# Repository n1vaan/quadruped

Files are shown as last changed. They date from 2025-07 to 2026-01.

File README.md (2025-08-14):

# Quadruped Robot

### Project Description

This is a smart quadruped robot dog that imitates the Boston Dynamics robot Spot. It uses inverse kinematics logic, along with visual input through cameras and quantitive measurements through an IMU to inform it's walking and movement algorithmns. 

### Why we made it

We set out to build a quadruped robot to better understand how complex systems like locomotion, balance, and perception work together in robotics. This project gave us the opportunity to apply concepts like inverse kinematics, sensor integration, and real-time control in a hands-on way. Building a walking robot also pushed us to think carefully about both mechanical design and software logic.

## Fully Assembled Prototype 
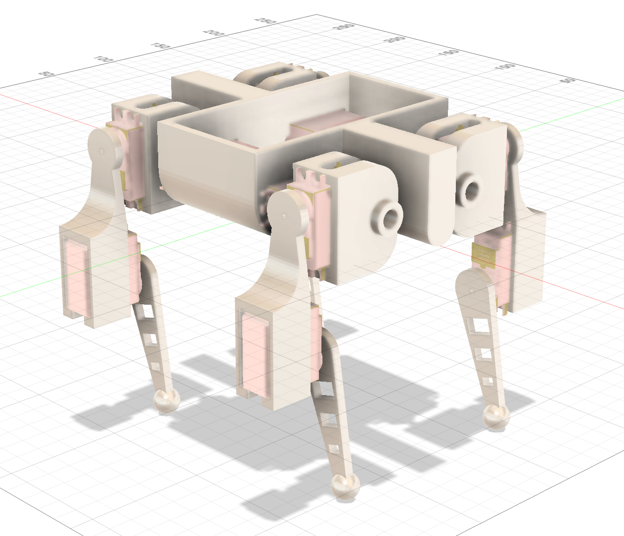
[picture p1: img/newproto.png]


## Rendered Prototype 
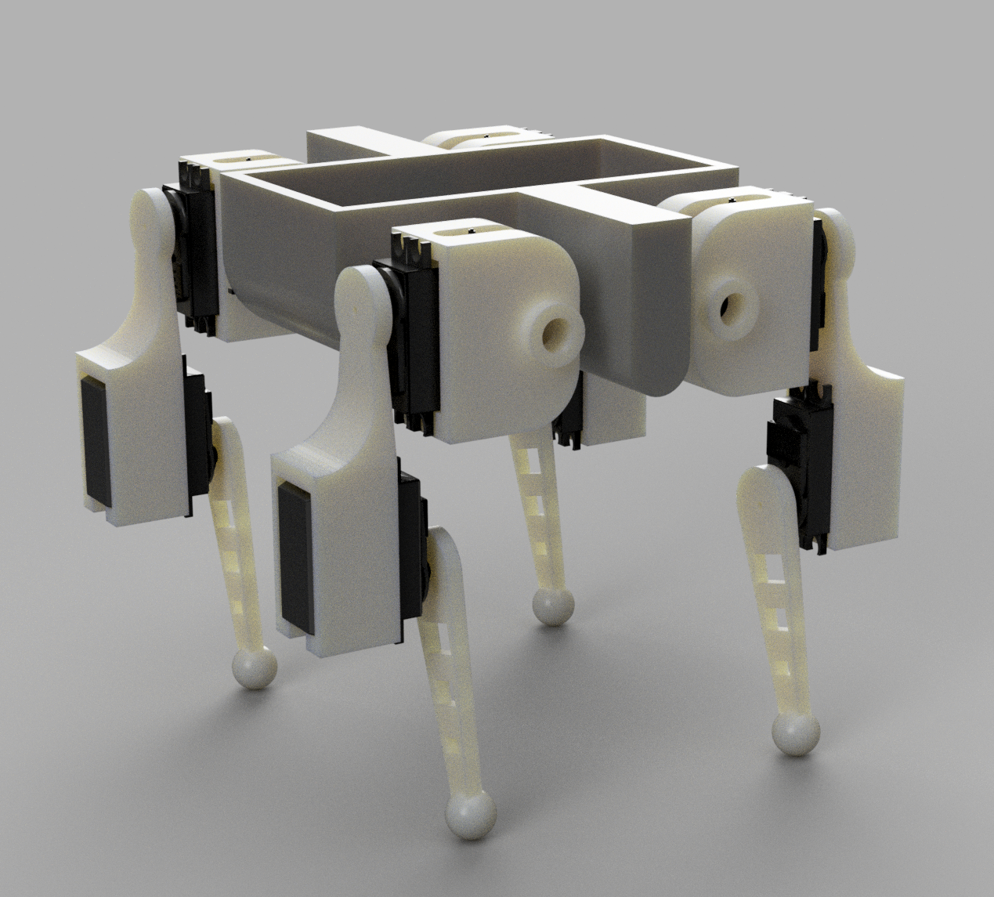
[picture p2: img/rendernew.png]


## Circuit 
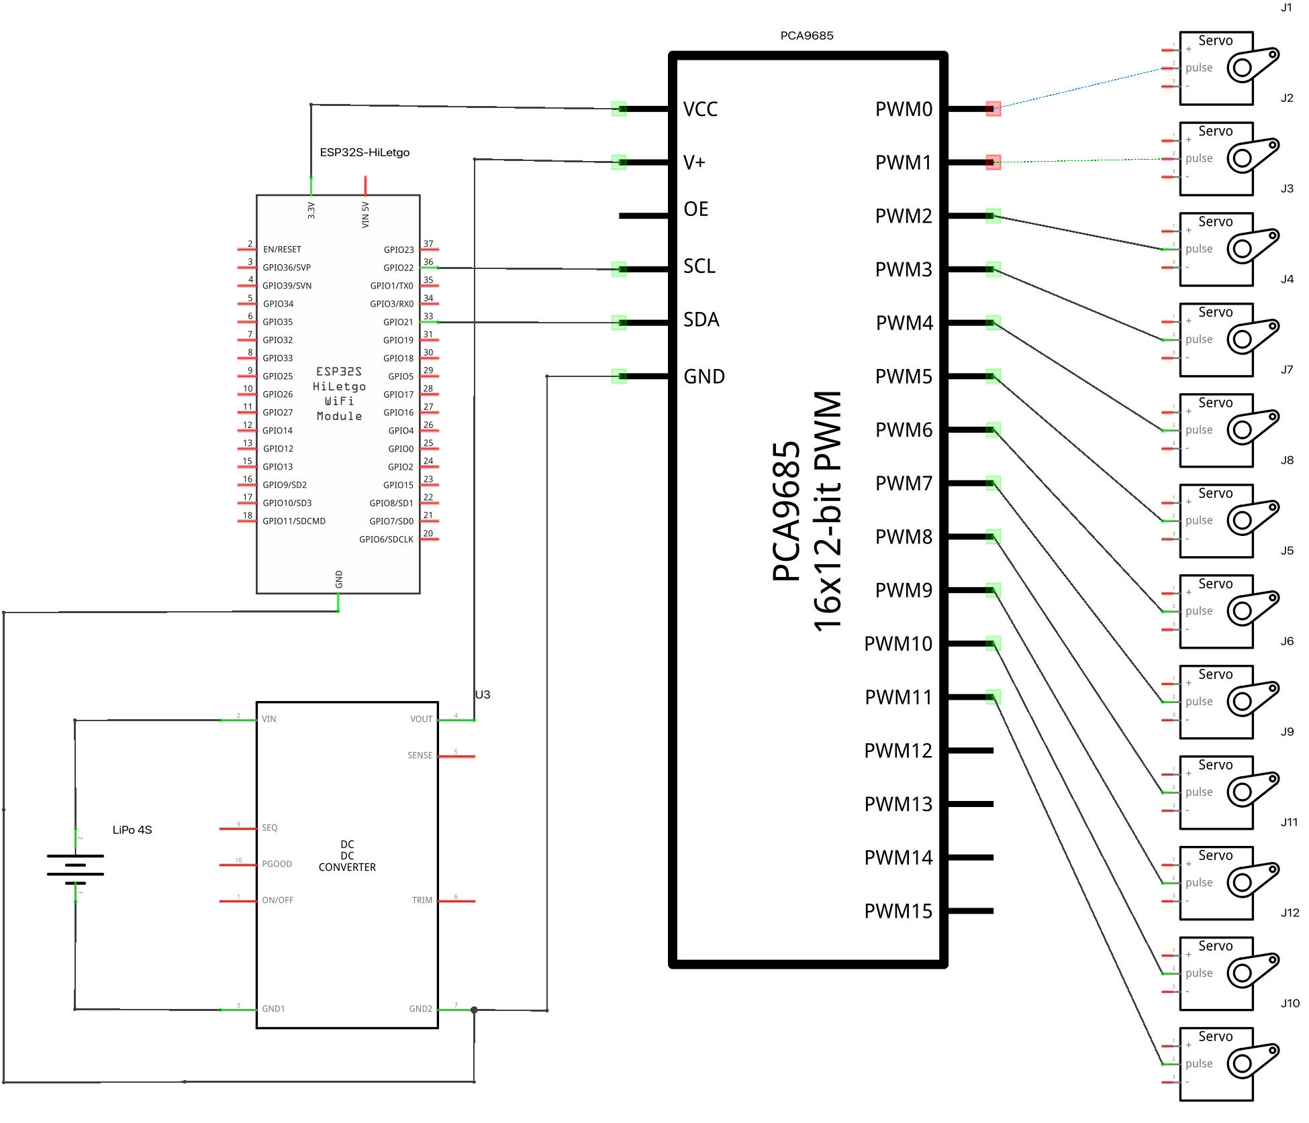
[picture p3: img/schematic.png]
Circuitry

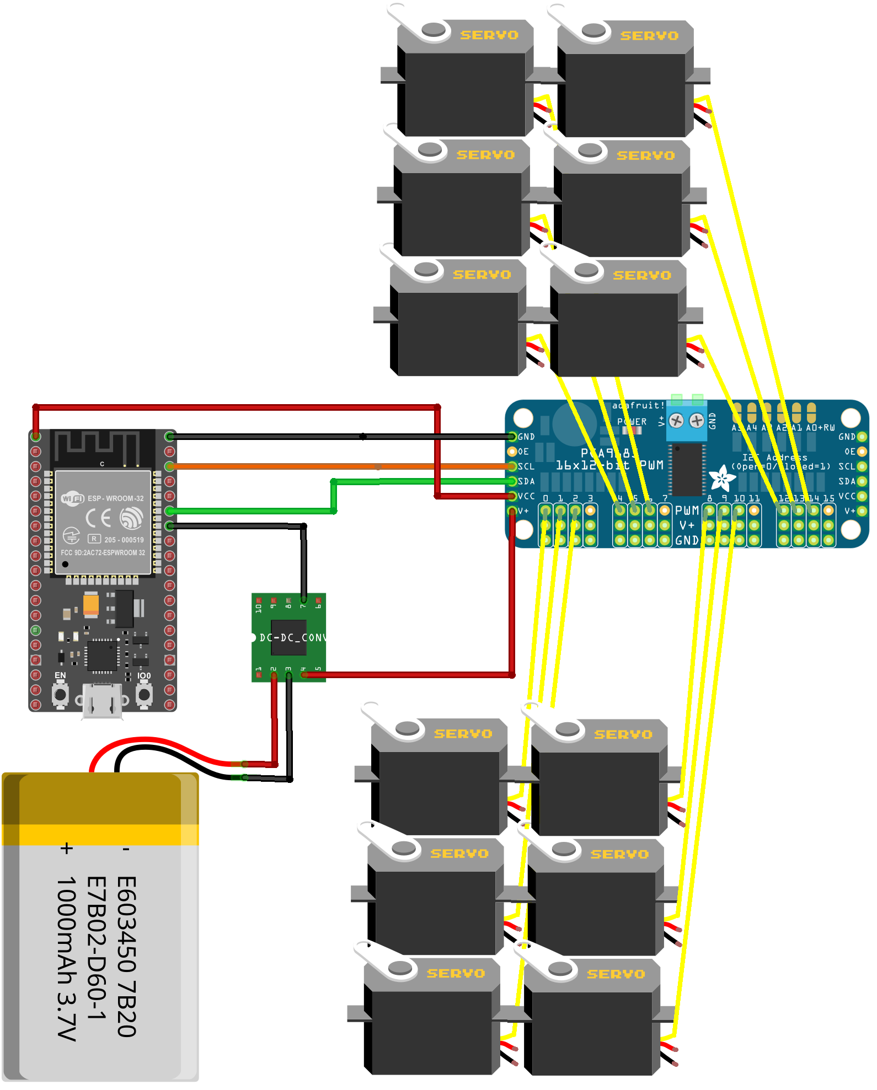
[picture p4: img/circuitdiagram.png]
Diagram


## Bill of Materials (BOM)

| Component | Quantity | Price Estimate | Link |
|---|---|---|---|
| MG996R Motors | 12 | $54 | [Amazon](https://www.amazon.com/6-Pack-MG996R-Torque-Digital-Helicopter/dp/B07MFK266B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) |
| PCA9685 (x2 is cheaper) | 1 | $14 | [Amazon](https://www.amazon.com/HiLetgo-PCA9685-Channel-12-Bit-Arduino/dp/B07BRS249H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) |
| 12V to 5V Voltage Transformer | 1 | $10 | [Amazon](https://www.amazon.com/VOLRANTISE-Converter-Voltage-Regulator-Transformer/dp/B09WZ9DC9W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)|
| Total | 14 | $78 | N/A |

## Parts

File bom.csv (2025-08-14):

Component | Quantity | Price Estimate | Link
MG996R Motors | 12 | $54 | https://www.amazon.com/6-Pack-MG996R-Torque-Digital-Helicopter/dp/B07MFK266B/ref=asc_df_B0BMM1G74B
PCA9685 | 1 | $14 | https://www.amazon.com/HiLetgo-PCA9685-Channel-12-Bit-Arduino/dp/B07BRS249H
12V to 5V Voltage Transformer | 1 | $10 | https://www.amazon.com/VOLRANTISE-Converter-Voltage-Regulator-Transformer/dp/B09WZ9DC9W
Total | 14 | $78 | N/A

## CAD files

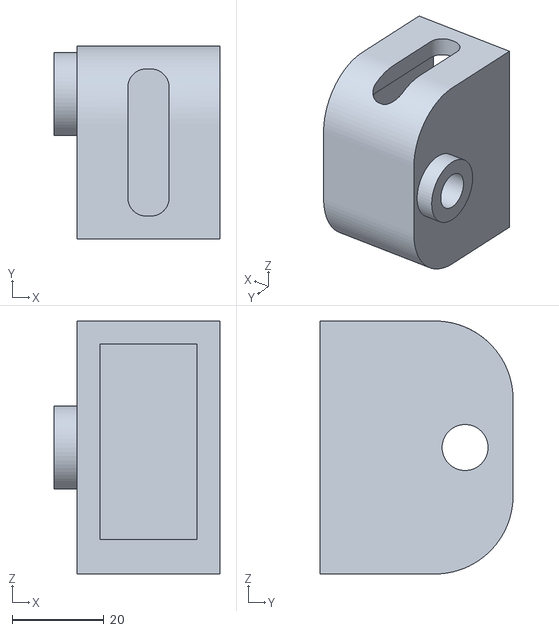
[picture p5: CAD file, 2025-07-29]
cad/stl/HipBraceNew2.stl
36.0 x 42.0 x 55.0

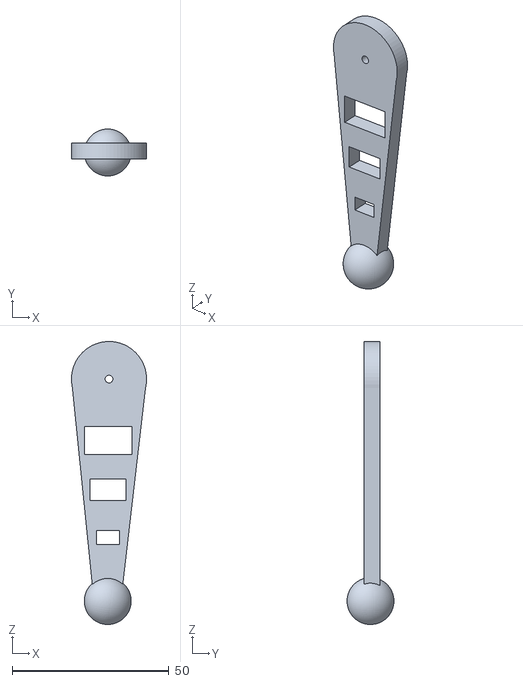
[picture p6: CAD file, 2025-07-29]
cad/stl/FinalLimbNew.stl
24.0 x 15.0 x 90.4

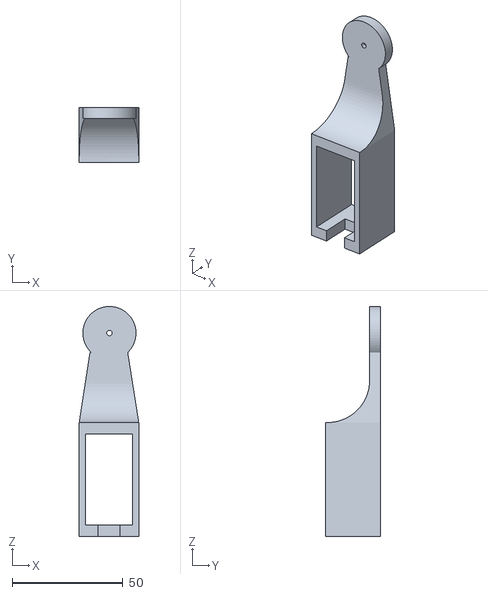
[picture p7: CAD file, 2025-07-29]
cad/stl/KneeBraceNew.stl
26.9 x 25.0 x 103.8

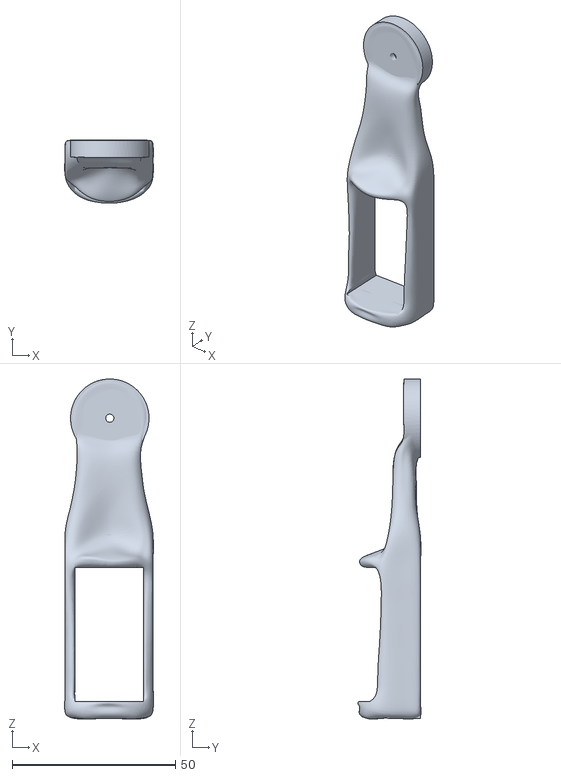
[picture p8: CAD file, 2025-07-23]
cad/stl/Kneebrace.stl
27.1 x 19.4 x 104.0

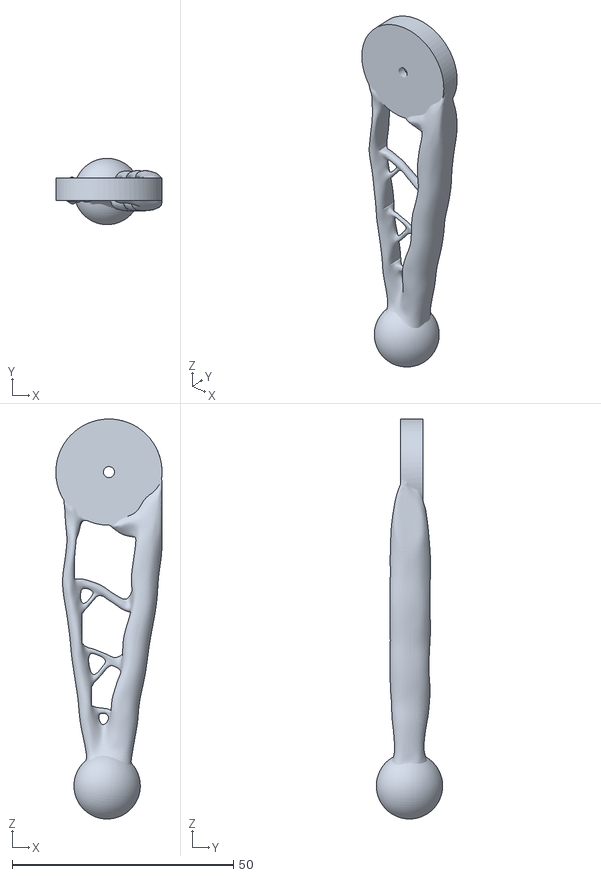
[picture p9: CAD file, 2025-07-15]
cad/stl/FinalLeg.stl
24.0 x 15.0 x 90.4

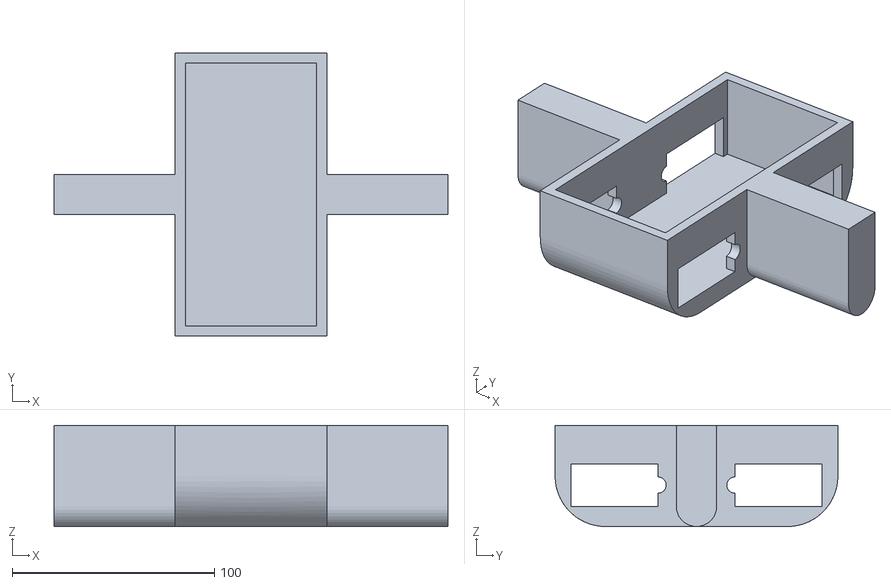
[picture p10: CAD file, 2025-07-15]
cad/stl/CenterNew.stl
195.0 x 140.0 x 50.0

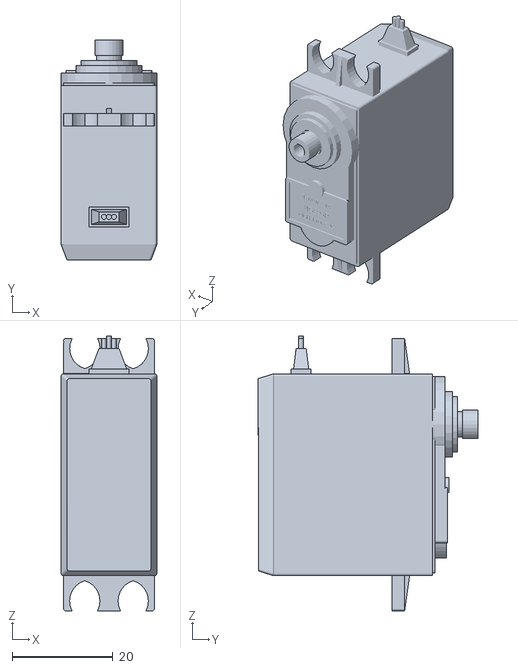
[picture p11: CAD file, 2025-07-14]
cad/stl/MG996RServo.stl
19.0 x 43.5 x 54.5

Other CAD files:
cad/FullAssembly.step
cad/stepindividual/KneeBraceNew.step
cad/stepindividual/HipBraceNew2.step
cad/stepindividual/HipBraceNew1.step
cad/stl/HipBraceNew1.stl
cad/stepindividual/FinalLimbNew.step
cad/stepindividual/CenterNew.step

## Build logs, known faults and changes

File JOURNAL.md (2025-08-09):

---
title: "12 DoF Autonomous Quadruped"
author: "Nivaan Kaushal"
description: "A 12-DOF robotic quadruped powered by an ESP32, utelizing inverse kinematics to aid movement. Includes camera, IMU for intelligent movement. "
created_at: "2025-07-01"
---

## Total Time Spent: ~35 hours   

### July 1st
Time Spent: ~3 hours  

Today I spent around 3 hours finalizing the electronics setup for the quadruped. I worked through the voltage and current requirements for all 12 servos, made sure the ESP32 would get clean power, and mapped out how everything would be connected. After a lot of calculations and comparing specs, I landed on a 2S LiPo battery, a 5V 10A buck converter, and a PCA9685 PWM driver to handle the servo control. This setup ensures that each servo will get appropriate power. I will need 12 MG996R servos, as they are high torque, allow angle setting, and also affordable.  Next, I aim to make a CAD design for the quadruped that is built around these components. 

Circuitry

### July 2nd
Time Spent: ~4 hours

Today I spent around 4 hours constructing the central enclosure for the quadruped. This was particularly challenging because I had to design it with the constraints of the motors and circuitry, maintaining enough space for all the components but also staying lightweight. I found an online model of the MG996R servos, which was particularly helpful when designing the enclosure rather than just using numerical measurements. I also planned servo placement; the 4 servos shown below serve as hips. I will have 4 more servos serving as rotation points for the leg, and 4 others serving as knee joints. Hopefully the servos have enough power to sustain this load. 

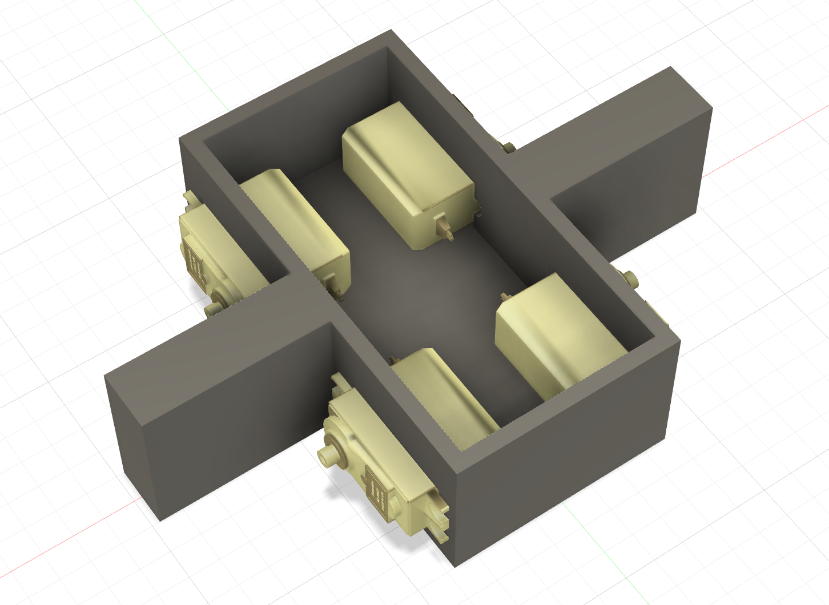
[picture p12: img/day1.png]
Day 1 Image


### July 3rd
Time Spent: ~5 hours

Today I spent around 5 hours designing the leg brace for the leg motor joints. This was especially time consuming because I learned to use a new tool: Fusion's Generative Design Tool. I first made a rough enclosure for the motor. This part was pretty easy. Then, I watched a tutorial on the generative design feature in Fusion. After watching it, I set the Preserve Geometry, Obstacle Geometry, and the Starting Shape. I ran several iterations of the Generative Design. After around 3 hours, I finally generated this really cool design that reduced weight while remaining structurally sound. I am really glad that I learned this new skill and will continue to use it on this project. 

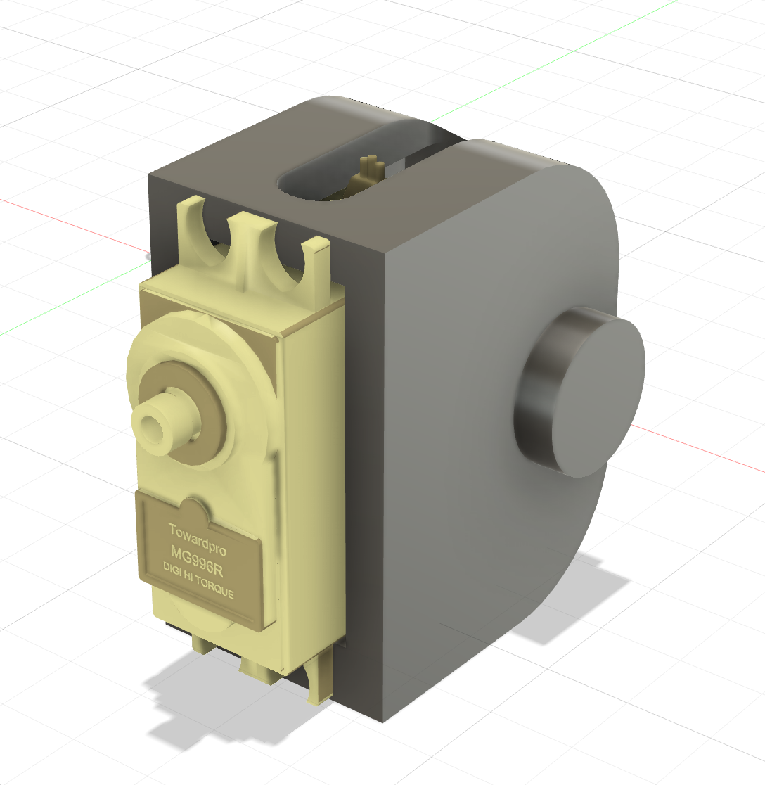
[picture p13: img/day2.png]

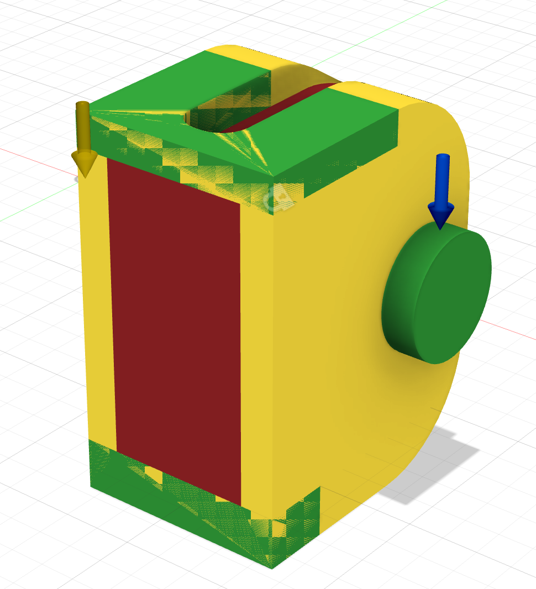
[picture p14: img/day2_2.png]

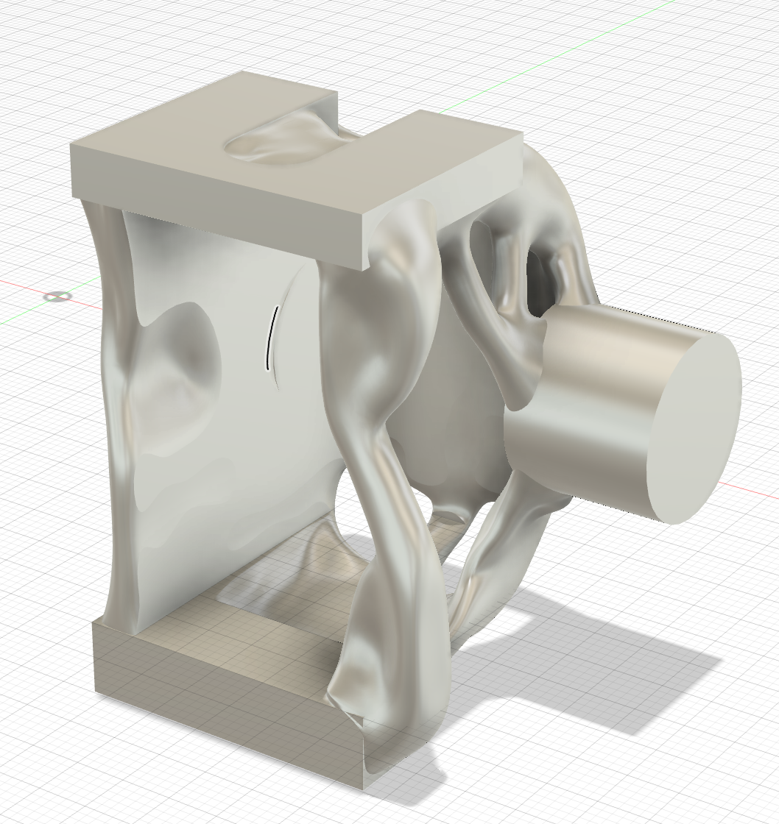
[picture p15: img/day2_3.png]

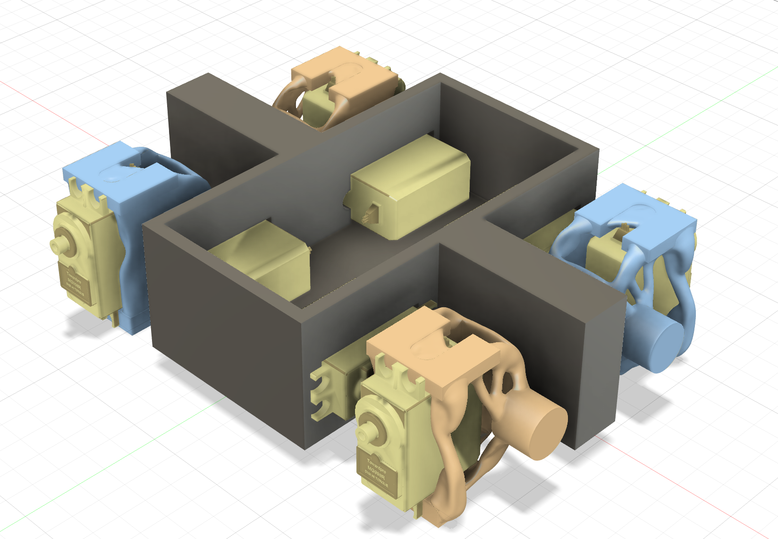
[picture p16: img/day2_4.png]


### July 6th
Time Spent: ~2 hours

Today I spent 2 hours designing the knee brace for the knee motor joints. This was much faster than last time because I had much more knowledge and experience with the Generative Design Tool. However, I had to run more simulations this time because it kept converging to a result that would result in too much structural strain. After I generated a design I was happy with, I assembled it all together. 

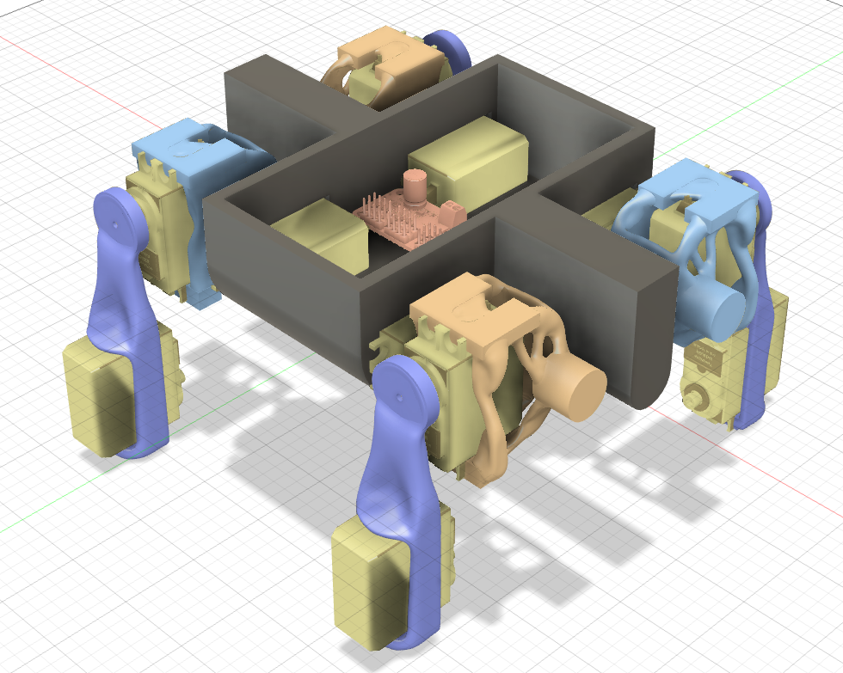
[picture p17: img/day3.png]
Day 3 Image


### July 8th
Time Spent: ~6 hours

Today I spent 6 hours designing the final joint for the legs. This took a considerable amount of time because I had to experiment a lot with obstacle conditions to provide a joint that was structurally sound. This joint is probably the one that needs the most structural integrity because it will carry all the weight from the quadruped and also be the joints that are walked on. In the end, I am really proud of how the result looks; I hope that it is also strong in real life. 

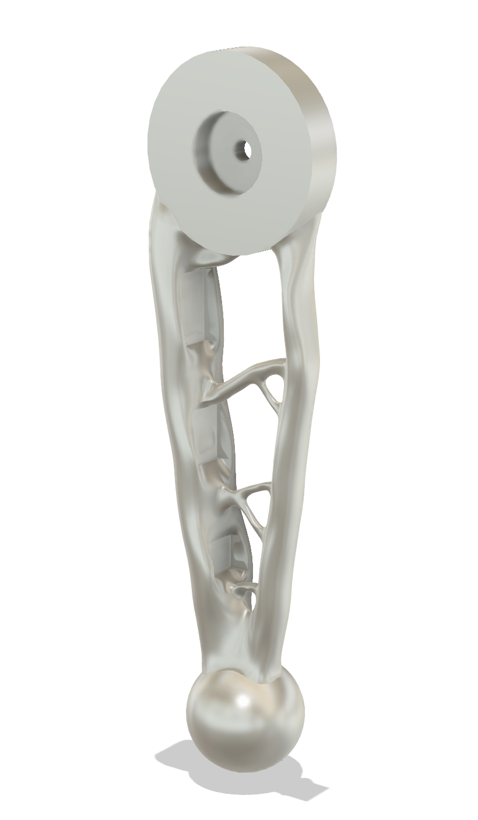
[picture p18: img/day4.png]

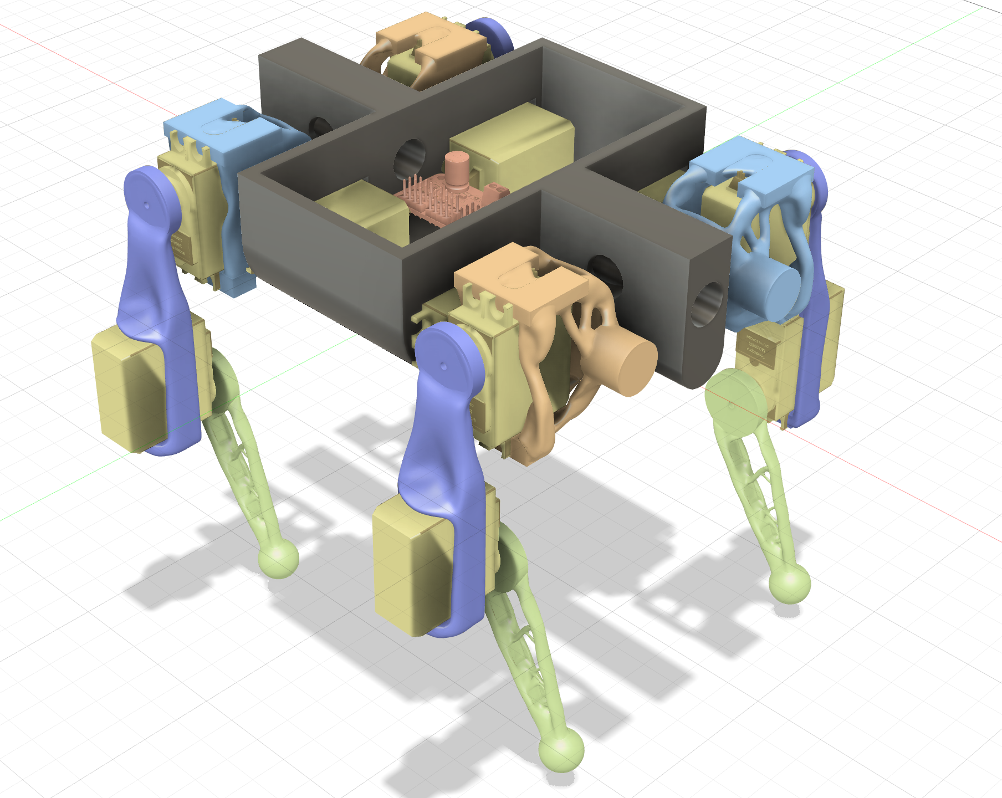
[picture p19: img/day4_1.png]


### July 29th 
Time Spent: ~4 hours

Following Ducc's advice on redesigning the parts on my own, today I spent some time redesigning the joints for the quadruped. The hardest part was minimizing the bulk and mass without generative design. I did so by running stress tests on each part, looking for particular areas that were extremely low in stress and were surrounded by low stressed areas, and removing them. Another challenge was making mounts for the screwholes and motor attachments. Since I don't have the motors in hand and their mounts, I made some approximations that I will fine tune once the motors arrive. 

I was particularly proud of the last leg joint. To add the spherical bottom that I have seen in many other prototypes, I used a Fusion form instead of the standard solids. Because of this method, I am now more comfortable with using Forms and have learned a new skill that I will definitely use in other projects. I then joined the form and solid to make a single unified part. Then, I used the Von Mises stress test to make some remove extrusions in areas that were particularly low in stress. 

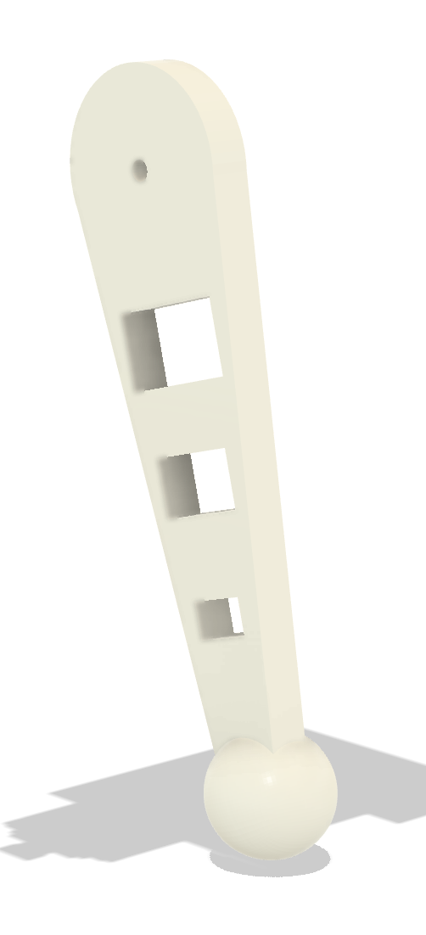
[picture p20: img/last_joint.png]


# July 30th 
Time Spent: ~3 hours

Today I redesigned the hip brace joint. First, I used my existing measurement of the motors as a guiding box that I had to build around for the part. I did this by first make a cube for the motor section. Then, I built around it by make sketch faces on the cube so that I could build around it. I found that this method was much harder becase filleting and having a fluid design between the faces was much harder to acheive, so I decided to first design the part and then use a remove extrusion for the motor section. I first made a basic cube design, and then filleted the back side so that there would be a larger range of motion for the joint. Then, I cut the whole for the motor, and also made another hole at the top to accomodate for the motor wires that generally stick out around 2 mm. Finally, I thickened the portions at the top and bottom of the motor slot so that I could screw the motor in. I was really happy with my progress today.  

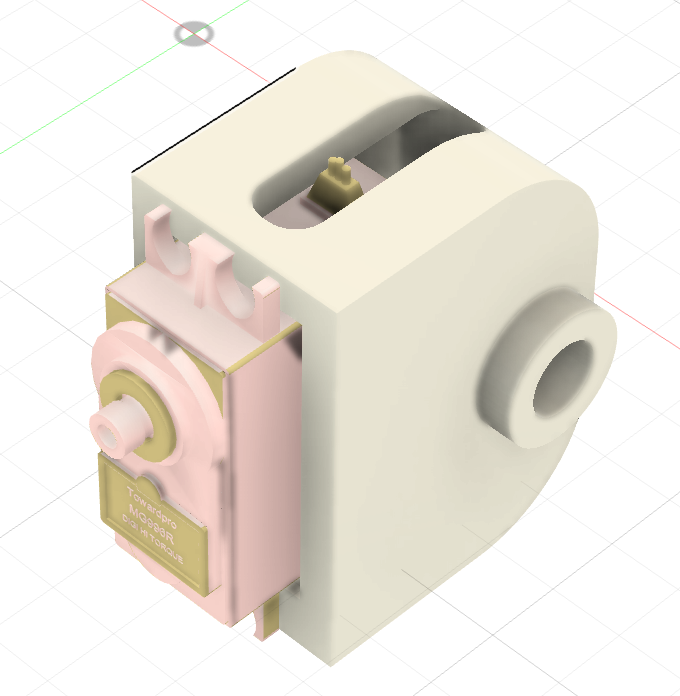
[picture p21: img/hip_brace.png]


# July 31st
Time Spent: ~3 hours

Today I made the central leg joint. Today was a much faster process because of the experiences and knowledge I had gained from yesterday and the day before. I started by make a log rectangular shape with a circle at the end for the leg. I didn't want it to be too long, as it would increase the moment of inertia and thus the torque required by the motor. Then, I extruded the bottom of the motor so that I could make a hole for the motor. Then, I followed yesterdays steps and thickened the tops and bottoms of the motor holes, both vertically and horizontally so that I could use screws. Finally, I made an arch between the top circular portion and the motor casing so that the design was more seamless. 

Then, I assembled the whole thing into one file. This was time consuming at first, but I realized that I could just use reflections and rotations instead of copy-pasting and dragging, rotating, etc. When I finally assembled the whole thing, I was satisfied with the result and actually preferred the design to the AI one. I did some rendering and was finally completed. 

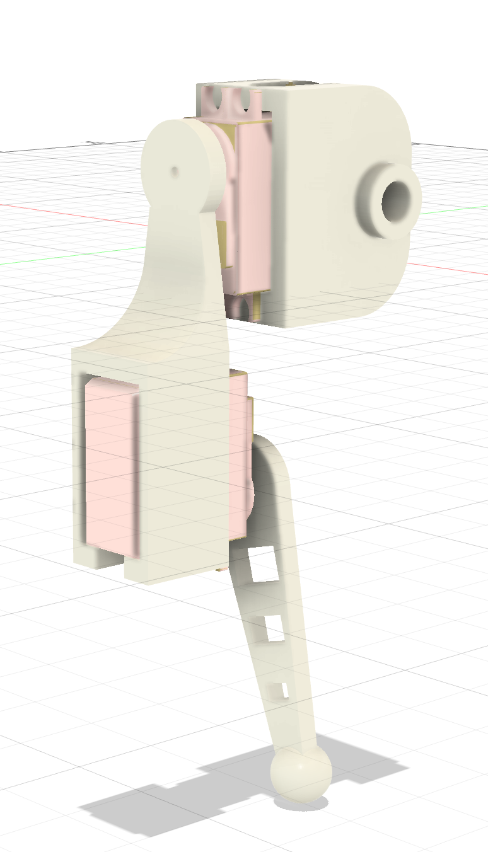
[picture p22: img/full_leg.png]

Day 5 Image

# August 8th
Time Spent: ~2 hours

Today I made my own inverse kinematics code for the quadruped's leg movements. To do so, I started off on paper and geometrically understood the point of inverse kinematics. It aims to find joint angles to get to a desired position (x,y). Using the law of cosines, I solved for the first angle, and based off of that angle, I solved for the second angle using the law of sines. It was really interesting seeing how the stuff we learnt in school was actually very useful in application. Then, to visualize the results, I tried inputting the results into desmos so that I could manipulate the desired position (x,y) and see the resulting joint angles visualized. This was much more challenging because I found out that arcsin is limited to the range of [-pi/2, pi/2], so I decided to use another approach that I found online using arctan2. Using this, I recreated my calculation system. I got the angles correct, and to connect the two "joints", I parameterized the vector and made sure to add the old vectors position as constants to make sure that they looked connected. It was a very long and arduous process, but I am happy I got it done; I now have my code basically layed out for me, and figuring it out on my own was especially rewarding. 

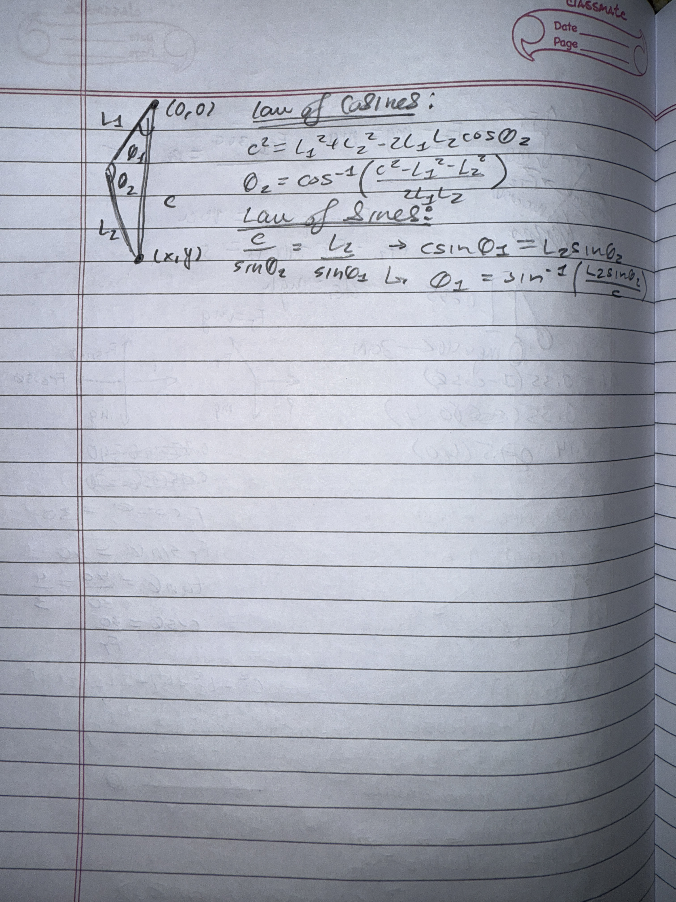
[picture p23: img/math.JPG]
Math

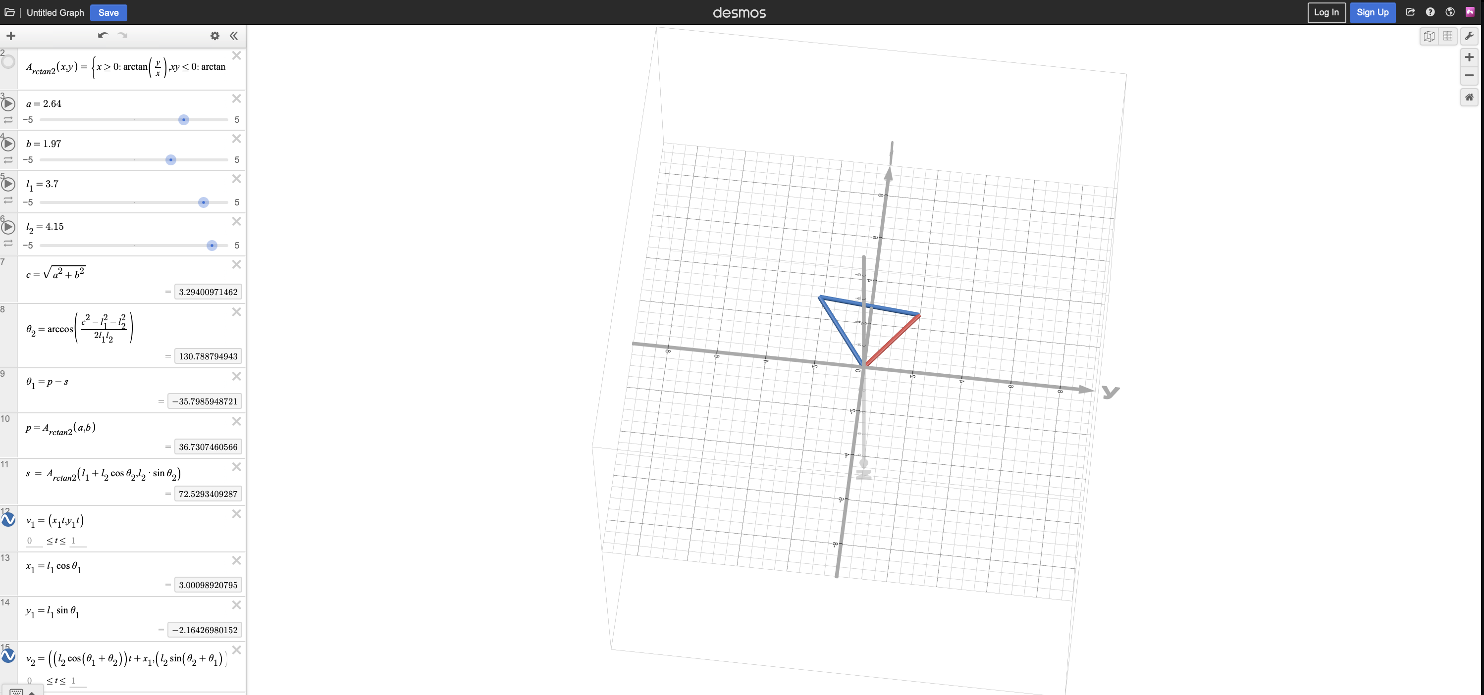
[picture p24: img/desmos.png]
Desmos


# August 9th
Time Spent: ~3 hours

Today I tried implementing the inverse kinematics math I did in code. This was pretty easy as all I had to do was rewrite the desmos code in C++'s syntax and wrap it in a method / function. Next, I tried to figure out the IMU logic. I had used an IMU before, but it was mainly for determining rotation in the XY Plane and not much beyond that. I looked at adafruit's documentation to understand more about it and wrote a method to extract values from  it. Then, I moved on to understanding how the PCA9685 works. This required me to code a method that converted the degree output from the inverseKinematics() function into Pulse Width Modulation signals. I wrote the method, but will have to calibrate it according to my motors when I receive them. Then, I wrote a basic function for leg movement, utelizing the inverseKinematics() and degreesToPulse() functions. Finally, I wrapped a sequence of leg movement functions in the walk() function, which I call in void loop. I will require a lot of fine tuning of the hyperparameters like l1, l2, and the motor ranges, but that will be easy once I receive the parts. I am really happy with my progress today because I was dreading the coding part, and am happy I got it over with. Now, hopefully my project is ready to be approved.

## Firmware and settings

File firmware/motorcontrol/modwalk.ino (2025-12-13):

#include <Servo.h>
#include <Wire.h>
#include <Adafruit_Sensor.h>
#include <Adafruit_BNO055.h>
#include <utility/imumaths.h>
#include <math.h>

Adafruit_BNO055 bno = Adafruit_BNO055(55);

Servo backHipRight;
Servo frontHipRight;
Servo frontHipLeft;
Servo backHipLeft;

const int L1 = 75; 
const int L2 = 80;

Servo backArmLeft;
Servo backArmRight;
Servo frontArmRight;
Servo frontArmLeft;

Servo frontKneeRight;
Servo frontKneeLeft;
Servo backKneeLeft;
Servo backKneeRight;

struct ServoMap {
  const char* name;
  int angle;        
};

ServoMap config[] = {
  {"backHipRight", 90},
  {"frontHipRight", 95},
  {"frontHipLeft", 100},
  {"backHipLeft", 80},
  {"backArmLeft", 100},
  {"backArmRight", 90},
  {"frontArmRight", 50},
  {"frontArmLeft", 90},
  {"frontKneeRight", 90},
  {"frontKneeLeft", 90},
  {"backKneeLeft", 15},
  {"backKneeRight", 90}
};

const int NUM_SERVOS = sizeof(config)/sizeof(config[0]);

int currentAngle[NUM_SERVOS];

const int pinBackHipRight = 2;
const int pinFrontHipRight = 3; 
const int pinFrontHipLeft = 4; 
const int pinBackHipLeft = 5;

const int pinBackArmLeft = 6;
const int pinBackArmRight = 7;
const int pinFrontArmRight = 8;
const int pinFrontArmLeft = 9;

const int pinFrontKneeRight = 10;
const int pinFrontKneeLeft = 11;
const int pinBackKneeLeft = 12;
const int pinBackKneeRight = 13;

bool setServoAngle(String name, int angle);
void applyConfig();


int getCurrentAngle(const char* name) {
  for (int i = 0; i < NUM_SERVOS; i++) {
    if (strcmp(config[i].name, name) == 0) {
      return currentAngle[i];
    }
  }
  return 90;
}

bool setServoAngle(String name, int angle) {

  // Move servo
  if      (name == "backHipRight")  backHipRight.write(angle);
  else if (name == "frontHipRight") frontHipRight.write(angle);
  else if (name == "frontHipLeft")  frontHipLeft.write(angle);
  else if (name == "backHipLeft")   backHipLeft.write(angle);
  else if (name == "backArmLeft")   backArmLeft.write(angle);
  else if (name == "backArmRight")  backArmRight.write(angle);
  else if (name == "frontArmRight") frontArmRight.write(angle);
  else if (name == "frontArmLeft")  frontArmLeft.write(angle);
  else if (name == "frontKneeRight") frontKneeRight.write(angle);
  else if (name == "frontKneeLeft")  frontKneeLeft.write(angle);
  else if (name == "backKneeLeft")   backKneeLeft.write(angle);
  else if (name == "backKneeRight")  backKneeRight.write(angle);
  else return false;

  for (int i = 0; i < NUM_SERVOS; i++) {
    if (strcmp(config[i].name, name.c_str()) == 0) {
      currentAngle[i] = angle;
      break;
    }
  }

  return true;
}

void applyConfig() {
  for (int i = 0; i < NUM_SERVOS; i++) {
    setServoAngle(config[i].name, config[i].angle);
  }
}

int getConfigAngle(const char* name) {
  for (int i = 0; i < NUM_SERVOS; i++) {
    if (strcmp(config[i].name, name) == 0) {
      return config[i].angle;
    }
  }
  return 90;  
}

void setGradualServo(String servo, int current, int angle, int delayTime, int offset) {
  int diff = angle - current;
  int stepDir = (diff >= 0) ? 1 : -1;
  int steps = abs(diff) / offset;

  for (int i = 0; i <= steps; i++) {
    int newAngle = current + stepDir * i * offset;
    setServoAngle(servo, newAngle);
    delay(delayTime);
  }

  setServoAngle(servo, angle);
}

void shiftCOM(String legName, int offset, int delayTime = 5) {

  if (legName == "frontLeft") {
    setGradualServo("frontHipLeft",  getCurrentAngle("frontHipLeft"),  getCurrentAngle("frontHipLeft")  + offset/2, delayTime, 1);
    setGradualServo("frontArmLeft",  getCurrentAngle("frontArmLeft"),  getCurrentAngle("frontArmLeft")  + offset/2, delayTime, 1);
    setGradualServo("frontKneeLeft",  getCurrentAngle("frontKneeLeft"),  getCurrentAngle("frontKneeLeft")  + offset/2, delayTime, 1);
  }

  else if (legName == "frontRight") {
    setGradualServo("frontHipRight", getCurrentAngle("frontHipRight"), getCurrentAngle("frontHipRight") - offset, delayTime, 1);
    setGradualServo("frontArmRight",  getCurrentAngle("frontArmRight"),  getCurrentAngle("frontArmRight")  + offset/2, delayTime, 1);
    setGradualServo("frontKneeRight",  getCurrentAngle("frontKneeRight"),  getCurrentAngle("frontKneeRight")  - offset/2, delayTime, 1);


  }

  else if (legName == "backLeft") {
    setGradualServo("backHipLeft",   getCurrentAngle("backHipLeft"),   getCurrentAngle("backHipLeft")   - offset, delayTime, 1);
    setGradualServo("backArmLeft",   getCurrentAngle("backArmLeft"),   getCurrentAngle("backArmLeft")   + offset, delayTime, 1);
    setGradualServo("backKneeLeft",   getCurrentAngle("backKneeLeft"),   getCurrentAngle("backKneeLeft")   + offset, delayTime, 1);
  }

  else if (legName == "backRight") {
    setGradualServo("backHipRight",  getCurrentAngle("backHipRight"),  getCurrentAngle("backHipRight")  + offset, delayTime, 1);
    setGradualServo("backArmRight",   getCurrentAngle("backArmRight"),   getCurrentAngle("backArmRight")   - offset, delayTime, 1);
    setGradualServo("backKneeRight",   getCurrentAngle("backKneeRight"),   getCurrentAngle("backKneeRight")   - offset, delayTime, 1);

  }
}

void walkForward(int steps, int delayTime, int dxFrontKnee, int dxBackKnee, int dxFrontArm, int dxBackArm) {
  for (int i = 0; i < steps; i++) {

    shiftCOM("backRight", 10);
    setServoAngle("frontKneeLeft", getCurrentAngle("frontKneeLeft") + dxFrontKnee);
    delay(delayTime);
    setServoAngle("frontArmLeft", getCurrentAngle("frontArmLeft") - dxFrontArm);
    delay(delayTime);
    shiftCOM("backRight", -10);

    shiftCOM("frontLeft", 5);
    setServoAngle("backKneeRight", getCurrentAngle("backKneeRight") - dxBackKnee);
    delay(delayTime);
    setServoAngle("backArmRight", getCurrentAngle("backArmRight") + dxBackArm);
    delay(delayTime);
    shiftCOM("frontLeft", -5);

    setServoAngle("frontKneeLeft", getConfigAngle("frontKneeLeft"));
    delay(delayTime);
    setServoAngle("frontArmLeft", getConfigAngle("frontArmLeft"));
    delay(delayTime);
    setServoAngle("backKneeRight", getConfigAngle("backKneeRight"));
    delay(delayTime);
    setServoAngle("backArmRight", getConfigAngle("backArmRight"));
    delay(delayTime);


    shiftCOM("backLeft", 15);
    setServoAngle("frontKneeRight", getCurrentAngle("frontKneeRight") - dxFrontKnee);
    delay(delayTime);
    setServoAngle("frontArmRight", getCurrentAngle("frontArmRight") + dxFrontArm);
    delay(delayTime);
    shiftCOM("backLeft", -15);

    shiftCOM("frontRight", 5);
    setServoAngle("backKneeLeft", getCurrentAngle("backKneeLeft") + dxBackKnee);
    delay(delayTime);
    setServoAngle("backArmLeft", getCurrentAngle("backArmLeft") - dxBackArm);
    delay(delayTime);
    shiftCOM("frontRight", -5);

    setServoAngle("frontKneeRight", getConfigAngle("frontKneeRight"));
    delay(delayTime);
    setServoAngle("frontArmRight", getConfigAngle("frontArmRight"));
    delay(delayTime);
    setServoAngle("backKneeLeft", getConfigAngle("backKneeLeft"));
    delay(delayTime);
    setServoAngle("backArmLeft", getConfigAngle("backArmLeft"));
    delay(delayTime);

    delay(delayTime * 2);
  }
}

void setup() {
  Serial.begin(9600);  
  while(!Serial);

  backHipRight.attach(pinBackHipRight);
  frontHipRight.attach(pinFrontHipRight);
  frontHipLeft.attach(pinFrontHipLeft);
  backHipLeft.attach(pinBackHipLeft);

  backArmLeft.attach(pinBackArmLeft);
  backArmRight.attach(pinBackArmRight);
  frontArmRight.attach(pinFrontArmRight);
  frontArmLeft.attach(pinFrontArmLeft);

  frontKneeRight.attach(pinFrontKneeRight);
  frontKneeLeft.attach(pinFrontKneeLeft);
  backKneeLeft.attach(pinBackKneeLeft);
  backKneeRight.attach(pinBackKneeRight);

  applyConfig();

  for (int i = 0; i < NUM_SERVOS; i++) {
    currentAngle[i] = config[i].angle;
  }

}

void handleSerial(String cmd) {
  Serial.println("CMD: " + cmd);

  if (cmd.startsWith("set ")) {
    cmd.remove(0, 4);
    int spaceIndex = cmd.indexOf(' ');
    if (spaceIndex == -1) {
      Serial.println("ERR: invalid set format");
      return;
    }
    String servo = cmd.substring(0, spaceIndex);
    int angle = cmd.substring(spaceIndex + 1).toInt();

    if (setServoAngle(servo, angle)) {
      Serial.println("OK SET " + servo + " = " + String(angle));
    } else {
      Serial.println("ERR: servo not found");
    }
  }

  else if (cmd.startsWith("get ")) {
    cmd.remove(0, 4);
    int angle = getCurrentAngle(cmd.c_str());
    Serial.println("ANGLE " + cmd + " = " + String(angle));
  }

  else if (cmd.startsWith("walk ")) {
    int steps = cmd.substring(5).toInt();
    walkForward(steps, 200, 10, 10, 20, 10);
    Serial.println("OK WALK " + String(steps));
  }

  else if (cmd == "reset") {
    applyConfig();
    Serial.println("OK RESET");
  }

  else if (cmd.startsWith("shift ")) {
    cmd.remove(0, 6); // remove "shift "
    int spaceIndex = cmd.indexOf(' ');
    if (spaceIndex == -1) {
      Serial.println("ERR: invalid shift format");
      return;
    }

    String leg = cmd.substring(0, spaceIndex);
    int offset = cmd.substring(spaceIndex + 1).toInt();

    shiftCOM(leg, offset);
    Serial.println("OK SHIFT " + leg + " by " + String(offset));
  }

  else if (cmd == "list") {
    for (int i = 0; i < NUM_SERVOS; i++) {
      Serial.println(String(config[i].name) + " = " + String(currentAngle[i]));
    }
  }

  else {
    Serial.println("ERR: unknown command");
  }

}

void loop() {
  if (Serial.available()) {
    String command = Serial.readStringUntil('\n');
    command.trim();
    handleSerial(command);
  } 
}

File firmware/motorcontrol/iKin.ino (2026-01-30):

#include <Servo.h>
#include <Wire.h>
#include <Adafruit_Sensor.h>
#include <Adafruit_BNO055.h>
#include <math.h>

class LegIK;

Adafruit_BNO055 bno = Adafruit_BNO055(55);

const float L1 = 75.0;   
const float L2 = 80.0;   

Servo backHipRight, frontHipRight, frontHipLeft, backHipLeft;
Servo backArmLeft, backArmRight, frontArmRight, frontArmLeft;
Servo frontKneeRight, frontKneeLeft, backKneeLeft, backKneeRight;

struct ServoMap {
  const char* name;
  int angle;
};

ServoMap config[] = {
  {"backHipRight", 90},
  {"frontHipRight", 90},
  {"frontHipLeft", 90},
  {"backHipLeft", 90},
  {"backArmLeft", 90},
  {"backArmRight", 90},
  {"frontArmRight", 90},
  {"frontArmLeft", 90},
  {"frontKneeRight", 90},
  {"frontKneeLeft", 90},
  {"backKneeLeft", 90},
  {"backKneeRight", 90}
};

const int NUM_SERVOS = sizeof(config) / sizeof(config[0]);

const int pinBackHipRight   = 2;
const int pinFrontHipRight  = 3;
const int pinFrontHipLeft   = 4;
const int pinBackHipLeft    = 5;
const int pinBackArmLeft    = 6;
const int pinBackArmRight   = 7;
const int pinFrontArmRight  = 8;
const int pinFrontArmLeft   = 9;
const int pinFrontKneeRight = 10;
const int pinFrontKneeLeft  = 11;
const int pinBackKneeLeft   = 12;
const int pinBackKneeRight  = 13;

int getZero(const char* name) {
  for (int i = 0; i < NUM_SERVOS; i++)
    if (!strcmp(config[i].name, name))
      return config[i].angle;
  return 90;
}

void setServo(const char* name, int angle) {
  angle = constrain(angle, 0, 180);
  if      (!strcmp(name,"backHipRight"))   backHipRight.write(angle);
  else if (!strcmp(name,"frontHipRight"))  frontHipRight.write(angle);
  else if (!strcmp(name,"frontHipLeft"))   frontHipLeft.write(angle);
  else if (!strcmp(name,"backHipLeft"))    backHipLeft.write(angle);
  else if (!strcmp(name,"backArmLeft"))    backArmLeft.write(angle);
  else if (!strcmp(name,"backArmRight"))   backArmRight.write(angle);
  else if (!strcmp(name,"frontArmRight"))  frontArmRight.write(angle);
  else if (!strcmp(name,"frontArmLeft"))   frontArmLeft.write(angle);
  else if (!strcmp(name,"frontKneeRight")) frontKneeRight.write(angle);
  else if (!strcmp(name,"frontKneeLeft"))  frontKneeLeft.write(angle);
  else if (!strcmp(name,"backKneeLeft"))   backKneeLeft.write(angle);
  else if (!strcmp(name,"backKneeRight"))  backKneeRight.write(angle);
}

void applyConfig() {
  for (int i = 0; i < NUM_SERVOS; i++)
    setServo(config[i].name, config[i].angle);
}

class LegIK {
public:
  float L1;
  float L2;
  const char* armName; 
  const char* kneeName;
  int armDir;
  int kneeDir;
  LegIK(float l1, float l2, const char* arm, const char* knee, int armd, int kneed){
    L1 = l1; 
    L2 = l2; 
    armName = arm;
    kneeName = knee;
    armDir = armd;
    kneeDir = kneed;
  }
  const char* getArm(){
    return armName;
  }
  const char* getKnee(){
    return kneeName; 
  }
  int getArmDir() {
    return armDir; 
  }
  int getKneeDir() {
    return kneeDir; 
  }
  bool solve(float x, float y, float &arm, float &knee) {
    float r = sqrt(x*x + y*y);
    if (r < 1.0) return false;

    float c1 = (L1*L1 + r*r - L2*L2) / (2*L1*r);
    float c2 = (L1*L1 + L2*L2 - r*r) / (2*L1*L2);

    c1 = constrain(c1, -1.0, 1.0);
    c2 = constrain(c2, -1.0, 1.0);

    float beta  = acos(c1);
    float alpha = acos(c2);
    float phi   = atan2(y, x);

    arm  = phi - beta;     
    knee = PI - alpha;     
    float arm1 = arm * 180.0 / PI; 
    float knee1 = knee * 180.0 / PI;
    return true;
  }
  void apply(float x, float y) {
    float armIK, kneeIK;
    if (!solve(x, y, armIK, kneeIK)) return;

    int armCmd =
      getZero(getArm()) + getArmDir() * (armIK * 180.0 / PI + 90);
    int kneeCmd =
      getZero(getKnee()) + getKneeDir() * (kneeIK) * 180.0 / PI;

    //     print(np.degrees(t1) + 90, np.degrees(t1+t2)+90)

    setServo(armName,  armCmd);
    setServo(kneeName, kneeCmd);
  }
};

// LegIK(float l1, float l2, const char* arm, const char* knee, int armd, int kneed){

LegIK frontLeftIK (L1, L2, "frontArmLeft", "frontKneeLeft", -1, +1);
LegIK frontRightIK(L1, L2, "frontArmRight", "frontKneeRight", +1, -1);
LegIK backLeftIK  (L1, L2, "backArmLeft", "backKneeLeft", -1, +1);
LegIK backRightIK (L1, L2, "backArmRight", "backKneeRight", +1, -1);

void setHipRoll(float rollDeg) {
  setServo("frontHipLeft",  getZero("frontHipLeft")  + rollDeg);
  setServo("backHipLeft",   getZero("backHipLeft")   + rollDeg);
  setServo("frontHipRight", getZero("frontHipRight") - rollDeg);
  setServo("backHipRight",  getZero("backHipRight")  - rollDeg);
}

void stand(float height) {
  float x = 0;
  float y = -height;

  frontLeftIK.apply(x, y);
  frontRightIK.apply(x, y);
  backLeftIK.apply(x, y);
  backRightIK.apply(x, y);
}

void tilt(float height, float delta, bool bias) {
  float x = 0;
  float y = -height;
  if (bias) {
    frontLeftIK.apply(x, y+delta);
    frontRightIK.apply(x, y+delta);
    backLeftIK.apply(x, y);
    backRightIK.apply(x, y);
  } else {
    frontLeftIK.apply(x, y);
    frontRightIK.apply(x, y);
    backLeftIK.apply(x, y+delta);
    backRightIK.apply(x, y+delta);
  }
}

void knees(float x, float y, bool bias) {
  if (bias) {
    frontLeftIK.apply(x, y);
    frontRightIK.apply(x, y);
  } else {
    backLeftIK.apply(x, y);
    backRightIK.apply(x, y);
  }
}

void walk(LegIK& leg,  float x0, float y0, float frequency, float duration, float xMax, float yMax, float del, float dt) {
  // frequency = b / 2pi
  float t = 0.0;
  float b = 2 * frequency * PI; 
  float xpos, ypos;
  while (t<duration) {
    t+=dt;
    xpos = x0 + xMax * sin(b * t);
    ypos = y0 + yMax * cos(b * t);

    Serial.print("X: ");
    Serial.println(xpos);

    Serial.print("Y: ");
    Serial.println(ypos);
    
    leg.apply(xpos, ypos);
    delay((int)(dt*1000));
  } 
}

void jump(int delta, int del) {
  
}

void setup() {
  Serial.begin(9600);

  backHipRight.attach(pinBackHipRight);
  frontHipRight.attach(pinFrontHipRight);
  frontHipLeft.attach(pinFrontHipLeft);
  backHipLeft.attach(pinBackHipLeft);
  backArmLeft.attach(pinBackArmLeft);
  backArmRight.attach(pinBackArmRight);
  frontArmRight.attach(pinFrontArmRight);
  frontArmLeft.attach(pinFrontArmLeft);
  frontKneeRight.attach(pinFrontKneeRight);
  frontKneeLeft.attach(pinFrontKneeLeft);
  backKneeLeft.attach(pinBackKneeLeft);
  backKneeRight.attach(pinBackKneeRight);

  applyConfig();

  if (bno.begin())
    bno.setExtCrystalUse(true);
}
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

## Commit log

2025-07-14 CAD Motor
    [MG996R_Servo_Model.stl]
2025-07-14 legbrace stl
2025-07-15 Final Leg Join
    [FinalLeg.stl, KneeBrace.stl]
2025-07-17 Added Assembly
2025-07-23 added updated stls
    [Center.stl, FinalLeg.stl, KneeBrace.stl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]
2025-07-29 New cad
    [Center.stl, CenterNew.step, CenterNew.stl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]
2025-07-31 removed gen
    [Center.stl, FinalLeg.stl, HipBrace1.stl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]
2025-08-08 assembly step
    [FullAssembly.step]
2025-08-08 Individual STEP
    [CenterNew.step, FinalLimbNew.step, HipBraceNew1.step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]
2025-08-12 New Assembly
    [CenterNew.stl, CompleteAssembly.step, FinalLimbNew.stl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]
2025-12-27 Add auto-leveling functionality with servos and IMU
    This file implements an auto-leveling system using servos and an IMU sensor. It includes functions for setting servo angles, getting current and configuration angles, and handling serial commands.
2026-01-30 Updated Inverse Kinematics
